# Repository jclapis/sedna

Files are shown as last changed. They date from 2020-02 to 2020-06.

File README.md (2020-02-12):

## Welcome to GitHub Pages

You can use the [editor on GitHub](https://github.com/jclapis/sedna/edit/master/README.md) to maintain and preview the content for your website in Markdown files.

Whenever you commit to this repository, GitHub Pages will run [Jekyll](https://jekyllrb.com/) to rebuild the pages in your site, from the content in your Markdown files.

### Markdown

Markdown is a lightweight and easy-to-use syntax for styling your writing. It includes conventions for

```markdown
Syntax highlighted code block

# Header 1
## Header 2
### Header 3

- Bulleted
- List

1. Numbered
2. List

**Bold** and _Italic_ and `Code` text

[Link](url) and ![Image](src)
```

For more details see [GitHub Flavored Markdown](https://guides.github.com/features/mastering-markdown/).

### Jekyll Themes

Your Pages site will use the layout and styles from the Jekyll theme you have selected in your [repository settings](https://github.com/jclapis/sedna/settings). The name of this theme is saved in the Jekyll `_config.yml` configuration file.

### Support or Contact

Having trouble with Pages? Check out our [documentation](https://help.github.com/categories/github-pages-basics/) or [contact support](https://github.com/contact) and we’ll help you sort it out.

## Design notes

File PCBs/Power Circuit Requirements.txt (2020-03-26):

Circuit requirements!

- An arbitrary 12v input
	- From a battery i'll make later
	- From the wall

- 12v line (motor, monitor)
- 7.2v line (camera)
- 5v line (pi, AMT22)
- 3.3v comes from the Pi for all of the other ICs
	- L6983CQTR for 12 and 7.2
	- L6983C50QTR for 5

- Measure rail voltages
	- MCP3208 (https://www.mouser.com/ProductDetail/Microchip-Technology/MCP3208T-CI-SL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)

- Current sensing shunt to see what the total current pull is
	- CS70P
		https://www.mouser.com/ProductDetail/STMicroelectronics/CS70P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
	- Resistor = 0.012 ohm, 500 mW
		https://www.mouser.com/ProductDetail/Vishay-Dale/WSK1206R0120FEA18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

- Thermometer
	- TC77-3.3MOA
		https://www.mouser.com/ProductDetail/Microchip-Technology/TC77-33MOA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

- Fuses?

NEED DECOUPLING CAPACITORS - 1uF ON EACH VDD PIN

SPRING TERMINALS: EATON EM2795 SERIES (Vertical is way cheaper for some reason)
	2-pin = EM279502V: https://www.mouser.com/ProductDetail/Bussmann-Eaton/EM279502V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
	The rest is stupidly expensive so just build it all out of these.

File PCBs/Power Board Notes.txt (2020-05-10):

** Assuming between 12.5v and 36v in, 400 kHz **

R_FILT = https://www.mouser.com/ProductDetail/Panasonic/ERA-6AEB101V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

=== Output Voltage Resistors ===
For 12v line:
	619 / 47 => 12.0446809v
	R1 = 619k https://www.mouser.com/ProductDetail/Panasonic/ERA-6AEB6193V?qs=sGAEpiMZZMvdGkrng054txAO1F77ZlZQbHrViC3uPIQ%3D
	R2 = 47k https://www.mouser.com/ProductDetail/Panasonic/ERA-6AEB473V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

For 7.2v line:
	680 / 91 => 7.20165v
	R1 = 680k = https://www.mouser.com/ProductDetail/Panasonic/ERA-6AEB684V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
	R2 = 91k = https://www.mouser.com/ProductDetail/Panasonic/ERA-6AEB913V?qs=sGAEpiMZZMvdGkrng054tysRcmITJKxoen6wp78Btbg%3D

For 5v line:
	402 / 82 => 5.017073v
	R1 = 402k = https://www.mouser.com/ProductDetail/Panasonic/ERA-6AEB4023V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
	R2 = 82k = https://www.mouser.com/ProductDetail/Panasonic/ERA-6AEB823V?qs=sGAEpiMZZMvdGkrng054tysRcmITJKxoBfxHTzMcu7Q%3D

=== Main Inductor ===
For 12v line:
	Min = 6.53977
	Max = 39.2430
	Mid = 22.89 uH (go with 22)
		https://www.mouser.com/ProductDetail/Pulse-Electronics/PA4343223NLT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

For 7.2v line:
	Min = -5.460 (so 0)
	Max = 27.243
	Mid = 13.6215 uH (go with 15)
		https://www.mouser.com/ProductDetail/Pulse-Electronics/PM4343153NLT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

For 5v line:
	Min = -10.9602 (so 0)
	Max = 21.7430
	Mid = 10.8715 uH (go with 10)
		https://www.mouser.com/ProductDetail/Pulse-Electronics/PM4343103NLT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

=== Output Capacitor ===
For 12v line:
	Min = 13.4 uF
	Max = 80 uF
	Mid = 46.7
		47 (26.5839) + 22 (18.5890) = 69 (45.1729)
		47 = https://www.mouser.com/ProductDetail/TDK/C5750X5R1C476M230KA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
		22 = https://www.mouser.com/ProductDetail/TDK/C5750X5R1E226M250KA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

For 7.2v line:
	Min = 22.3 uF
	Max = 133.3 uF
	Mid = 77.8
		47 (37.9989) + 47 (37.9989) = 94 (75.9978)
		47 = https://www.mouser.com/ProductDetail/TDK/C5750X5R1C476M230KA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

For 5v line:
	Min = 32.16 uF
	Max = 192 uF
	Mid = 112.08
		47 (43.3823) + 47 (43.3823) = 94 (86.7646), good enough
		47 = https://www.mouser.com/ProductDetail/TDK/C5750X5R1C476M230KA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

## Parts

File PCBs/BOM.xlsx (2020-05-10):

Totals
Part | Model # | Link | Total
C_BOOT | CGA4J2X7R1H104K125AA | https://www.mouser.com/ProductDetail/TDK/CGA4J2X7R1H104K125AA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 | 3
C_FILT and C_VIN | CGA4J3X7R1H105K125AB | https://www.mouser.com/ProductDetail/TDK/CGA4J3X7R1H105K125AB | 9
C_IN | CGA5L3X5R1H106K160AB | https://www.mouser.com/ProductDetail/TDK/CGA5L3X5R1H106K160AB | 3
47uF C_OUT | C5750X5R1C476M230KA | https://www.mouser.com/ProductDetail/TDK/C5750X5R1C476M230KA | 5
22uF C_OUT | C5750X5R1E226M250KA | https://www.mouser.com/ProductDetail/TDK/C5750X5R1E226M250KA | 1
C_VCC | CGA4J2X7R1C105K125AA | https://www.mouser.com/ProductDetail/TDK/CGA4J2X7R1C105K125AA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 | 3
5v Inductor | PM4343.103NLT | https://www.mouser.com/ProductDetail/Pulse-Electronics/PM4343103NLT | 1
7.2v Inductor | PM4343.153NLT | https://www.mouser.com/ProductDetail/Pulse-Electronics/PM4343153NLT | 1
12v Inductor | PA4343.223NLT | https://www.mouser.com/ProductDetail/Pulse-Electronics/PA4343223NLT | 1
Power Connectors | EM279502V | https://www.mouser.com/ProductDetail/Bussmann-Eaton/EM279502V | 6
L6983 | L6983CQTR | https://www.mouser.com/ProductDetail/STMicroelectronics/L6983CQTR | 3
5v FBH Resistor | ERA-6AEB4023V | https://www.mouser.com/ProductDetail/Panasonic/ERA-6AEB4023V | 1
5v FBL Resistor | ERA-6AEB823V | https://www.mouser.com/ProductDetail/Panasonic/ERA-6AEB823V?qs=sGAEpiMZZMvdGkrng054tysRcmITJKxoBfxHTzMcu7Q%3D | 1
7.2v FBH Resistor | ERA-6AEB684V | https://www.mouser.com/ProductDetail/Panasonic/ERA-6AEB684V | 1
7.2v FBL Resistor | ERA-6AEB913V | https://www.mouser.com/ProductDetail/Panasonic/ERA-6AEB913V?qs=sGAEpiMZZMvdGkrng054tysRcmITJKxoen6wp78Btbg%3D | 1
12v FBH Resistor | ERA-6AEB6193V | https://www.mouser.com/ProductDetail/Panasonic/ERA-6AEB6193V?qs=sGAEpiMZZMvdGkrng054txAO1F77ZlZQbHrViC3uPIQ%3D | 1
12v FBL Resistor | ERA-6AEB473V | https://www.mouser.com/ProductDetail/Panasonic/ERA-6AEB473V | 1
R_FILT | ERA-6AEB101V | https://www.mouser.com/ProductDetail/Panasonic/ERA-6AEB101V | 3
R_PGOOD | ERA-6AEB105V | https://www.mouser.com/ProductDetail/Panasonic/ERA-6AEB105V | 3

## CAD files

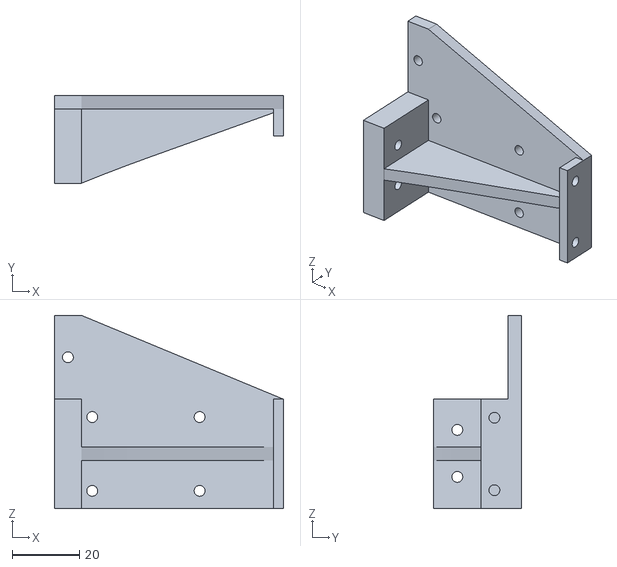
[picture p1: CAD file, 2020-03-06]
CAD Models/Focusing Assembly/Coupling Hub.stl
68.2 x 26.1 x 57.6

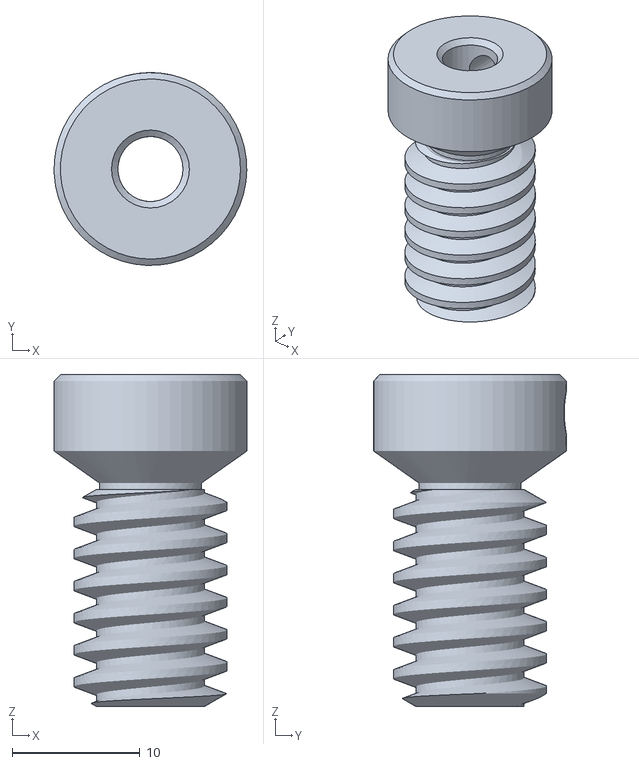
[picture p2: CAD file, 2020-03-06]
CAD Models/Focusing Assembly/Worm.stl
15.1 x 15.1 x 26.0

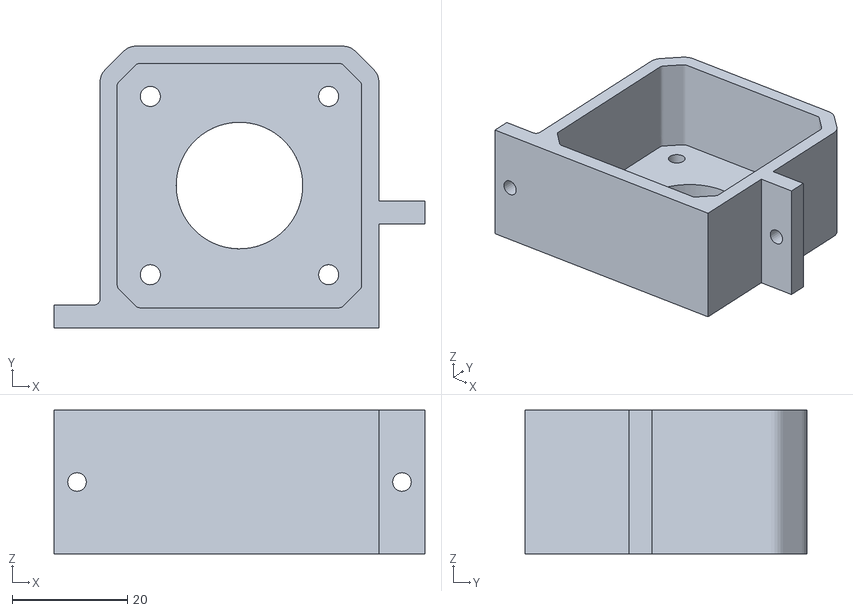
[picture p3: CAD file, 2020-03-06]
CAD Models/Focusing Assembly/Motor Housing.stl
64.5 x 49.0 x 25.0

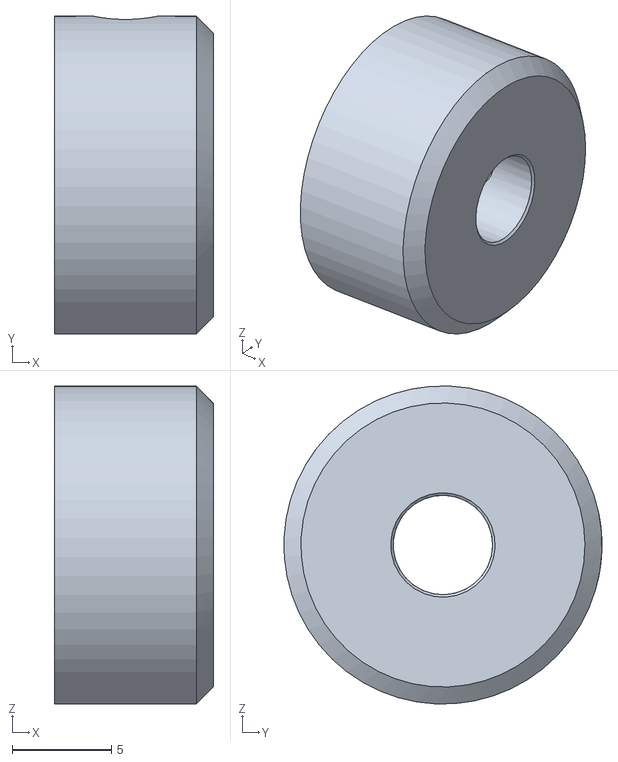
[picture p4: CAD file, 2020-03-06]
CAD Models/Focusing Assembly/Spur Gear Back.stl
8.00 x 16.0 x 16.0

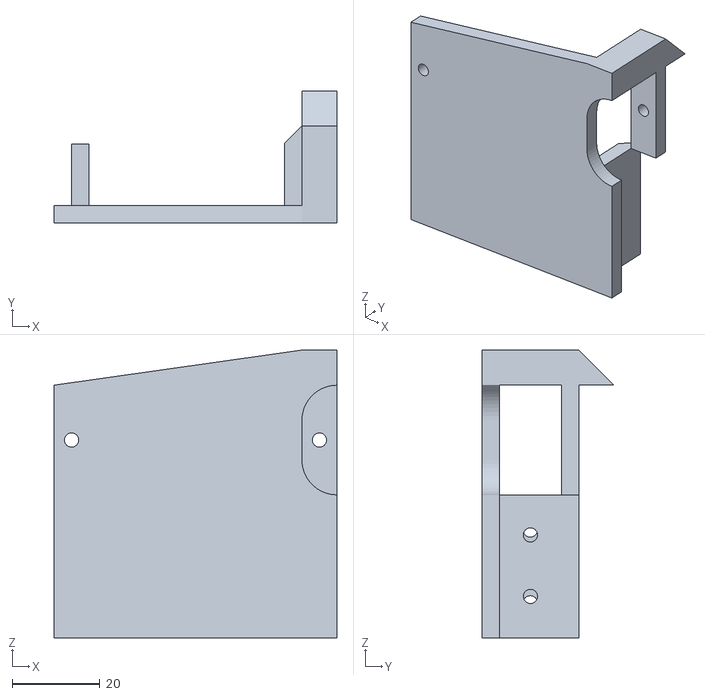
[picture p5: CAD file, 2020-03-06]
CAD Models/Focusing Assembly/Base Plate.stl
64.5 x 30.1 x 65.6

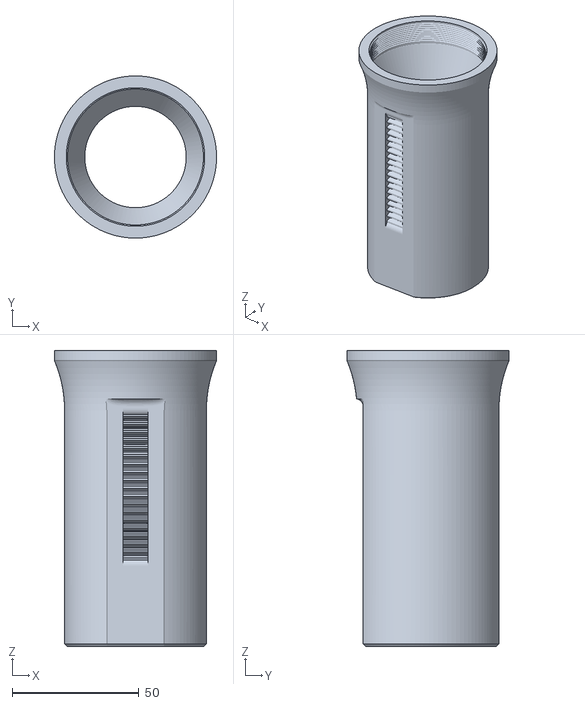
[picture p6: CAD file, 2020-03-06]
CAD Models/Focusing Assembly/Optical Tube.stl
64.0 x 64.0 x 116.8

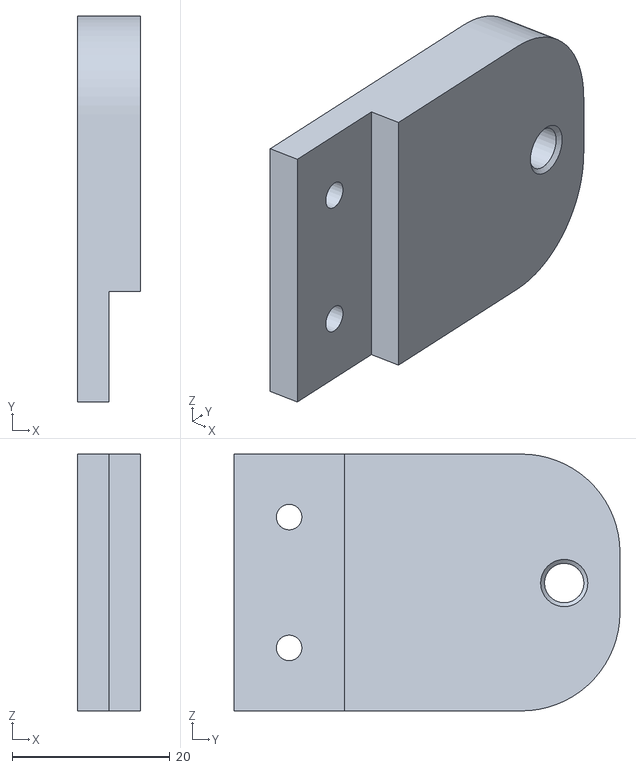
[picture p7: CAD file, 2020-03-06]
CAD Models/Focusing Assembly/Retainer Arm.stl
8.00 x 49.0 x 32.6

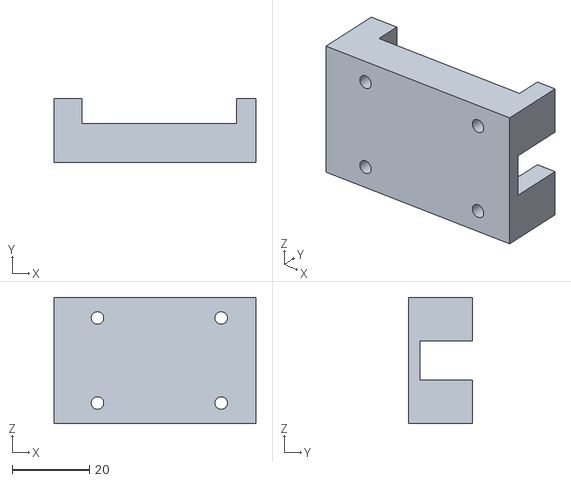
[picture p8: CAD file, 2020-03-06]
CAD Models/Focusing Assembly/Telescope Attachment.stl
52.2 x 16.5 x 32.6

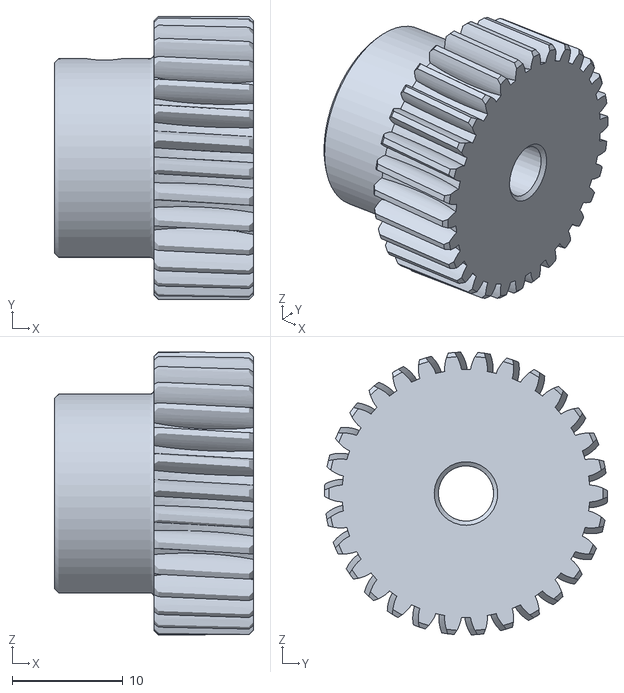
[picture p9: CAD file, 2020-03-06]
CAD Models/Focusing Assembly/Worm Gear.stl
18.0 x 25.6 x 25.6

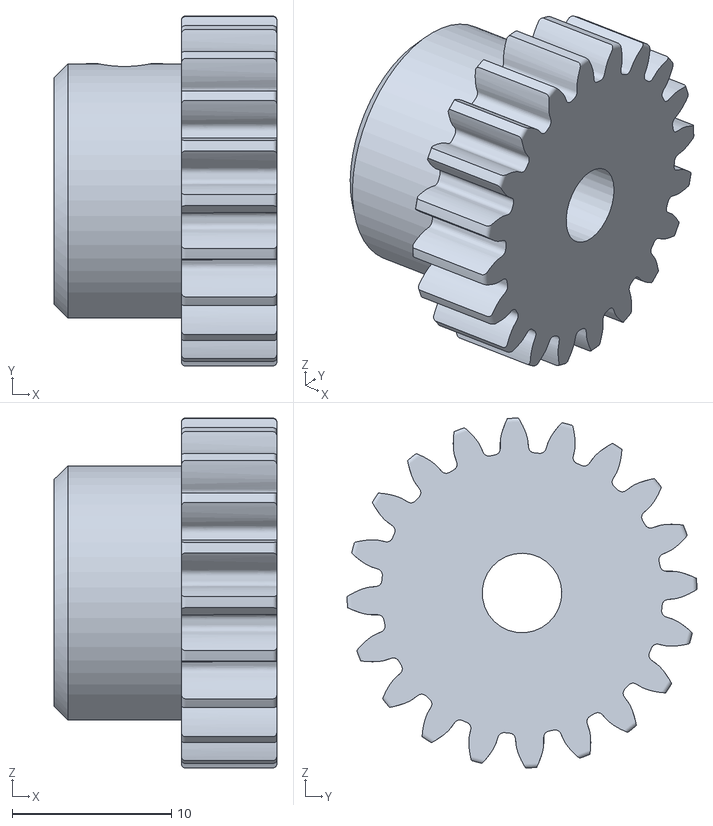
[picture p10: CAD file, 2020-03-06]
CAD Models/Focusing Assembly/Spur Gear.stl
14.0 x 22.0 x 22.0

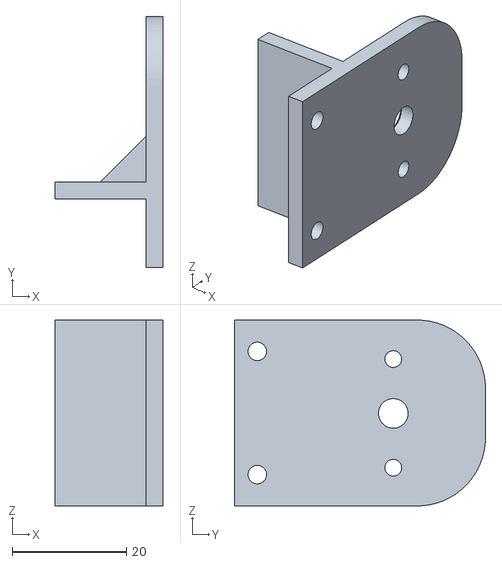
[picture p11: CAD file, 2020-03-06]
CAD Models/Focusing Assembly/AMT22 Bracket.stl
19.0 x 44.0 x 32.6

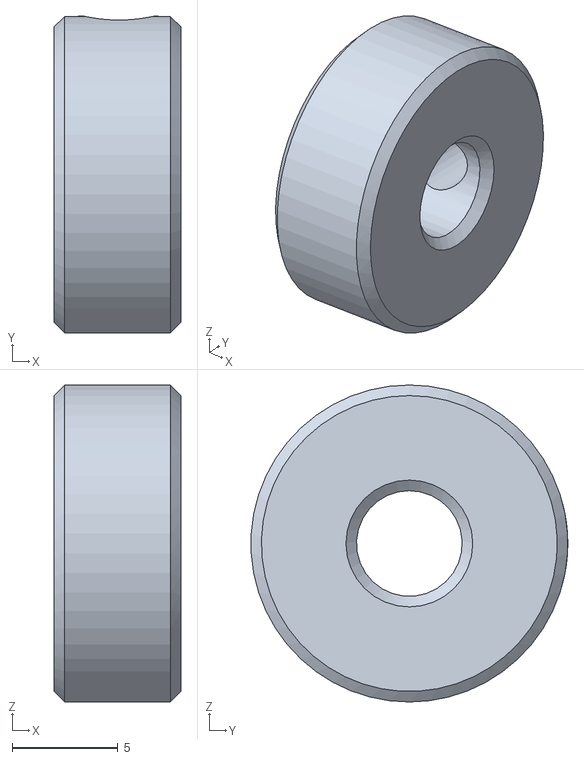
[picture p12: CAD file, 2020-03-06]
CAD Models/Focusing Assembly/Drive Shaft Washer.stl
6.00 x 15.0 x 15.0

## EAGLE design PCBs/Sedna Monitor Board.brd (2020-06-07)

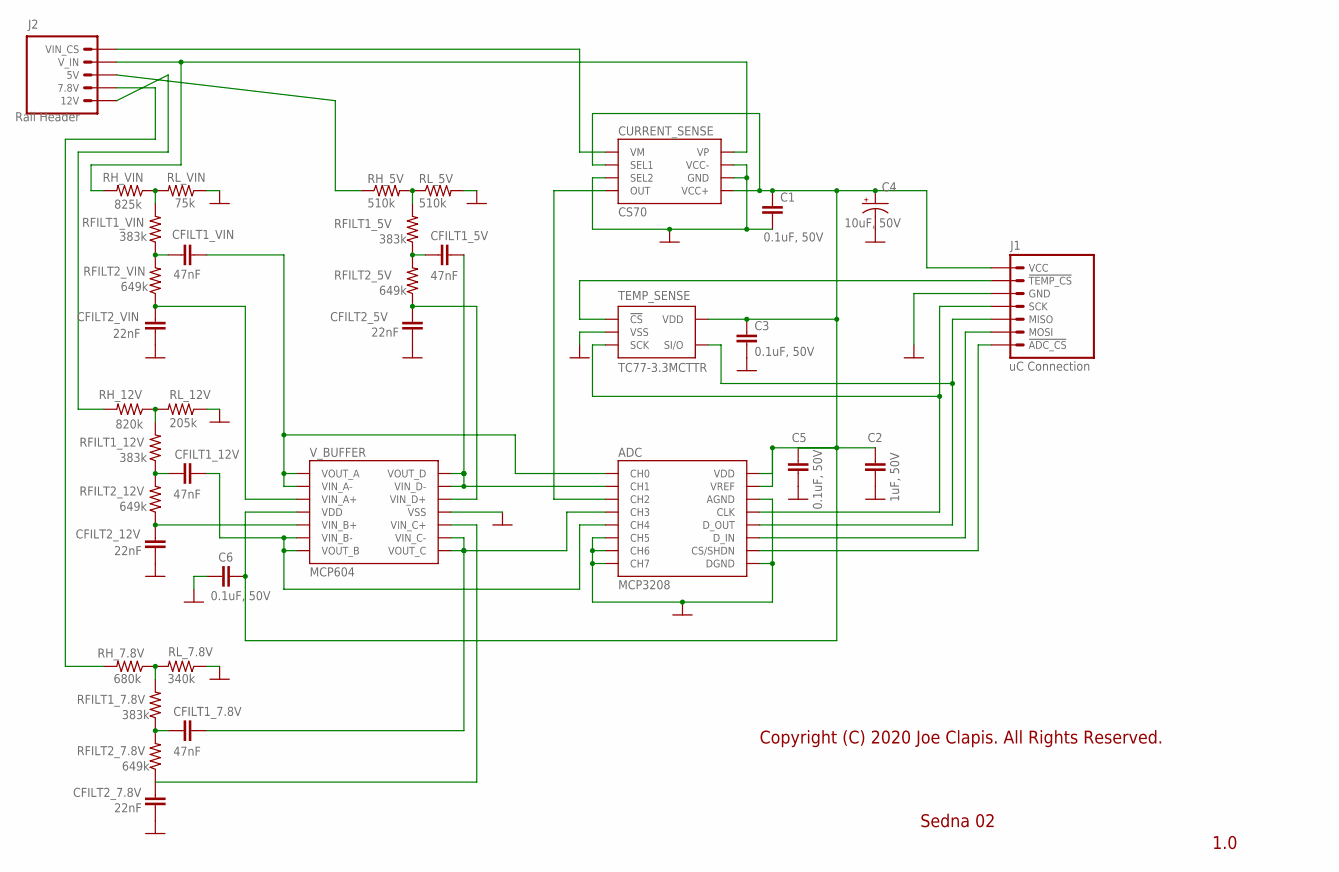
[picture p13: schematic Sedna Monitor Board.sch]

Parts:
ADC: MCP3208; MICROCHIP_SOIC-16_SL
C1, C3, C5, C6: 0.1uF, 50V; C0805
C2: 1uF, 50V; C0805
C4: 10uF, 50V; PANASONIC-SMD-CAP-SV-D
CFILT1_5V, CFILT1_7.8V, CFILT1_12V, CFILT1_VIN: 47nF; C0805
CFILT2_5V, CFILT2_7.8V, CFILT2_12V, CFILT2_VIN: 22nF; C0805
CURRENT_SENSE: CS70; TSSOP8
J1: uC Connection; 1X07
J2: Rail Header; 1X05
RFILT1_5V, RFILT1_7.8V, RFILT1_12V, RFILT1_VIN: 383k; R0805
RFILT2_5V, RFILT2_7.8V, RFILT2_12V, RFILT2_VIN: 649k; R0805
RH_5V: 510k; R0805
RH_7.8V: 680k; R0805
RH_12V: 820k; R0805
RH_VIN: 825k; R0805
RL_5V: 510k; R0805
RL_7.8V: 340k; R0805
RL_12V: 205k; R0805
RL_VIN: 75k; R0805
TEMP_SENSE: TC77-3.3MCTTR; MICROCHIP_SOT-23_5_OT
V_BUFFER: MCP604; MICROCHIP_TSSOP-14_ST

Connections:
ADC_CS: ADC.10 (CS/SHDN), J1.7 (!ADC_CS)
CS_OUT: ADC.3 (CH2), CURRENT_SENSE.4 (OUT)
GND: ADC.6 (CH5), ADC.7 (CH6), ADC.8 (CH7), ADC.9 (DGND), ADC.14 (AGND), C1.2, C2.2, C3.2, C4.GND (-), C5.2, C6.2, CFILT2_5V.1, CFILT2_7.8V.1, CFILT2_12V.1, CFILT2_VIN.1, CURRENT_SENSE.3 (SEL2), CURRENT_SENSE.6 (GND), CURRENT_SENSE.7 (VCC-), J1.3 (GND), RL_5V.2, RL_7.8V.1, RL_12V.1, RL_VIN.1, TEMP_SENSE.2 (VSS), V_BUFFER.11 (VSS)
MOSI: ADC.11 (D_IN), J1.6 (MOSI)
unnamed: ADC.12 (D_OUT), J1.5 (MISO), TEMP_SENSE.4 (SI/O)
unnamed: CURRENT_SENSE.1 (VM), J2.1 (VIN_CS)
unnamed: CURRENT_SENSE.8 (VP), J2.2 (V_IN), RH_VIN.2
unnamed: J2.4 (7.8V), RH_7.8V.2
unnamed: J2.3 (5V), RH_5V.1
unnamed: RFILT1_12V.2, RH_12V.1, RL_12V.2
unnamed: CFILT2_VIN.2, RFILT2_VIN.1, V_BUFFER.3 (VIN_A+)
unnamed: CFILT1_VIN.1, RFILT1_VIN.1, RFILT2_VIN.2
unnamed: J2.5 (12V), RH_12V.2
unnamed: RFILT1_VIN.2, RH_VIN.1, RL_VIN.2
unnamed: CFILT2_12V.2, RFILT2_12V.1, V_BUFFER.5 (VIN_B+)
unnamed: CFILT1_7.8V.2, RFILT1_7.8V.1, RFILT2_7.8V.2
unnamed: CFILT2_7.8V.2, RFILT2_7.8V.1, V_BUFFER.10 (VIN_C+)
unnamed: RFILT1_7.8V.2, RH_7.8V.1, RL_7.8V.2
unnamed: CFILT1_12V.1, RFILT1_12V.1, RFILT2_12V.2
unnamed: RFILT1_5V.2, RH_5V.2, RL_5V.1
unnamed: CFILT1_5V.2, RFILT1_5V.1, RFILT2_5V.2
unnamed: CFILT2_5V.2, RFILT2_5V.1, V_BUFFER.12 (VIN_D+)
SCK: ADC.13 (CLK), J1.4 (SCK), TEMP_SENSE.3 (SCK)
TC77_CS: J1.2 (!TEMP_CS), TEMP_SENSE.1 (!CS)
VDD: ADC.15 (VREF), ADC.16 (VDD), C1.1, C2.1, C3.1, C4.VDD (+), C5.1, C6.1, CURRENT_SENSE.2 (SEL1), CURRENT_SENSE.5 (VCC+), J1.1 (VCC), TEMP_SENSE.5 (VDD), V_BUFFER.4 (VDD)
VOUT_A: ADC.1 (CH0), CFILT1_VIN.2, V_BUFFER.1 (VOUT_A), V_BUFFER.2 (VIN_A-)
VOUT_B: ADC.5 (CH4), CFILT1_12V.2, V_BUFFER.6 (VIN_B-), V_BUFFER.7 (VOUT_B)
VOUT_C: ADC.4 (CH3), CFILT1_7.8V.1, V_BUFFER.8 (VOUT_C), V_BUFFER.9 (VIN_C-)
VOUT_D: ADC.2 (CH1), CFILT1_5V.1, V_BUFFER.13 (VIN_D-), V_BUFFER.14 (VOUT_D)

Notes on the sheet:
Sedna 02
1.0
Copyright (C) 2020 Joe Clapis. All Rights Reserved.

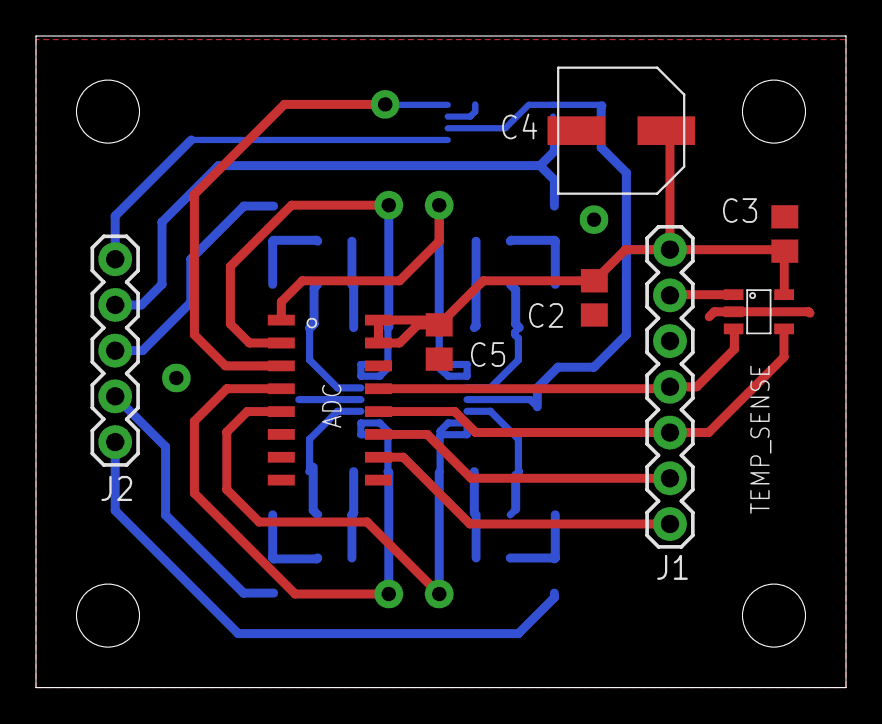
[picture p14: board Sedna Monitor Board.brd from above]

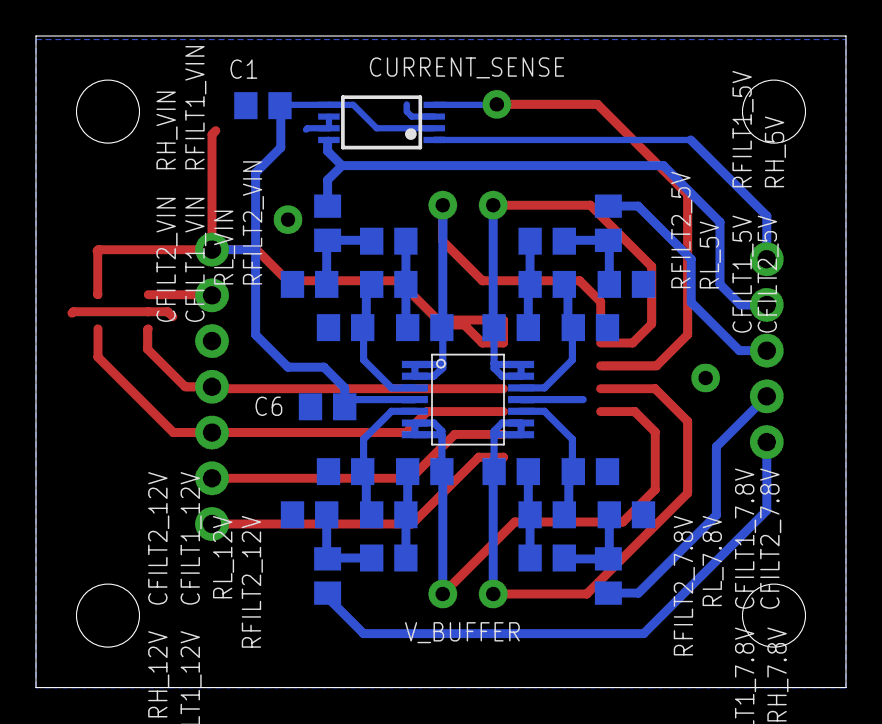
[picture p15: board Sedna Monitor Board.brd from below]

Board: 2 copper layers, 45.0 x 36.2 mm, 36 parts (28 on the bottom side), 29 nets.

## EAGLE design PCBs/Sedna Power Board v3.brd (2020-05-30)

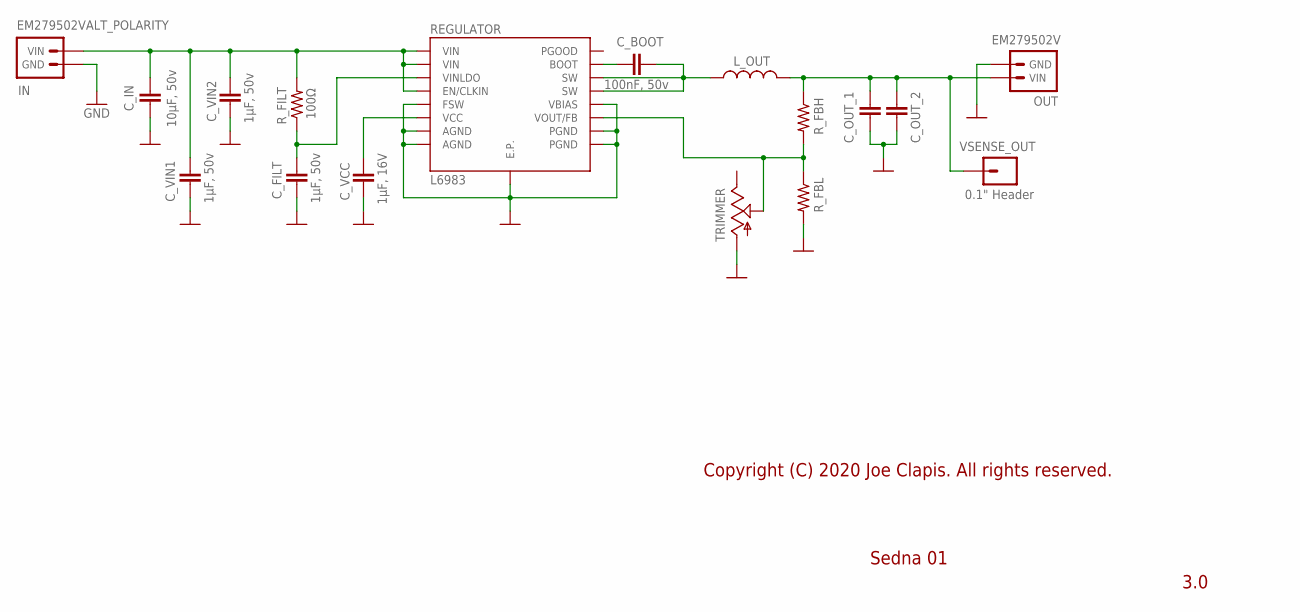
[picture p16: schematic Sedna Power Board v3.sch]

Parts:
C_BOOT: 100nF, 50v; C0805
C_FILT: 1μF, 50v; C0805
C_IN: 10μF, 50v; C1206
C_OUT_1, C_OUT_2: TDK_C2220_5750
C_VCC: 1μF, 16V; C0805
C_VIN1, C_VIN2: 1μF, 50v; C0805
IN: EM279502VALT_POLARITY; EM279502V
L_OUT: PA4343_FP2
OUT: EM279502V
REGULATOR: L6983
R_FBH: R-US_R0805; R0805
R_FBL: R-US_R0805; R0805
R_FILT: 100Ω; R0805
TRIMMER: BOURNS_3361S
VSENSE_OUT: 0.1" Header; 1X01

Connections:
C_BOOT: C_BOOT.1, REGULATOR.11_BOOT (BOOT)
FB: REGULATOR.7_FB/VOUT (VOUT/FB), R_FBH.2, R_FBL.1, TRIMMER.2 (S)
GND: C_FILT.2, C_IN.2, C_OUT_1.2, C_OUT_2.2, C_VCC.2, C_VIN1.2, C_VIN2.2, IN.1A (GND), IN.1B (GND), OUT.2A (GND), OUT.2B (GND), REGULATOR.3_AGND (AGND), REGULATOR.6_VBIAS (VBIAS), REGULATOR.8_FSW (FSW), REGULATOR.10_AGND (AGND), REGULATOR.13_PGND (PGND), REGULATOR.16_PGND (PGND), REGULATOR.E.P., R_FBL.2, TRIMMER.1 (A)
SW_OUT: C_BOOT.2, L_OUT.1, REGULATOR.14_SW (SW), REGULATOR.15_SW (SW)
VCC: C_VCC.1, REGULATOR.9_VCC (VCC)
VINLDO: C_FILT.1, REGULATOR.2_VINLDO (VINLDO), R_FILT.1
V_IN: C_IN.1, C_VIN1.1, C_VIN2.1, IN.2A (VIN), IN.2B (VIN), REGULATOR.1_VIN (VIN), REGULATOR.4_EN/CLKIN (EN/CLKIN), REGULATOR.12_VIN (VIN), R_FILT.2
V_OUT: C_OUT_1.1, C_OUT_2.1, L_OUT.2, OUT.1A (VIN), OUT.1B (VIN), R_FBH.1, VSENSE_OUT.1

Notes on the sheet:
Sedna 01
3.0
Copyright (C) 2020 Joe Clapis. All rights reserved.

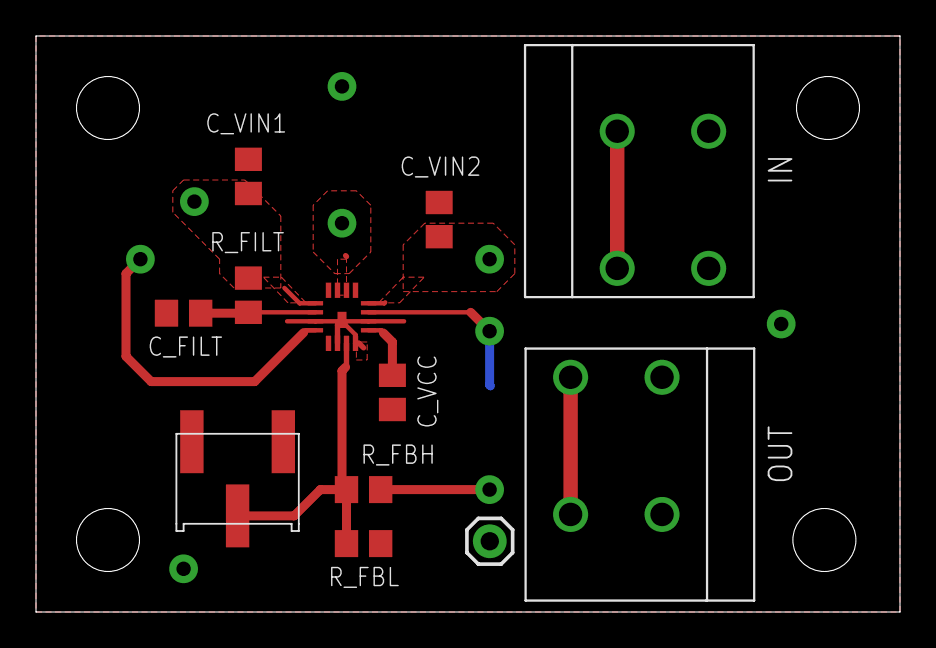
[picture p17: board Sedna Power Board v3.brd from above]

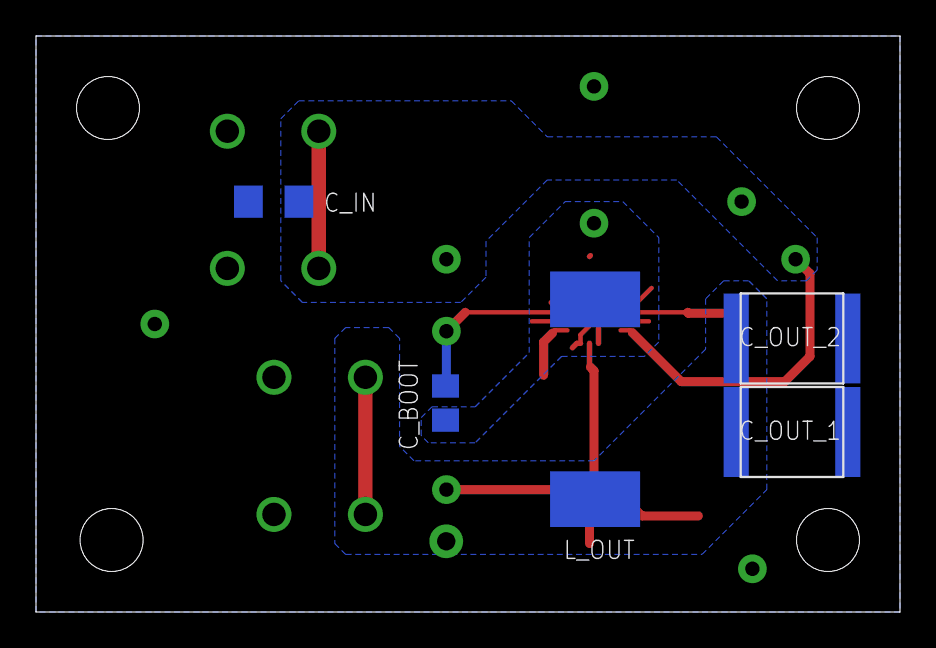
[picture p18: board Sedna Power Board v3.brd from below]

Board: 2 copper layers, 48.0 x 32.0 mm, 17 parts (5 on the bottom side), 8 nets.

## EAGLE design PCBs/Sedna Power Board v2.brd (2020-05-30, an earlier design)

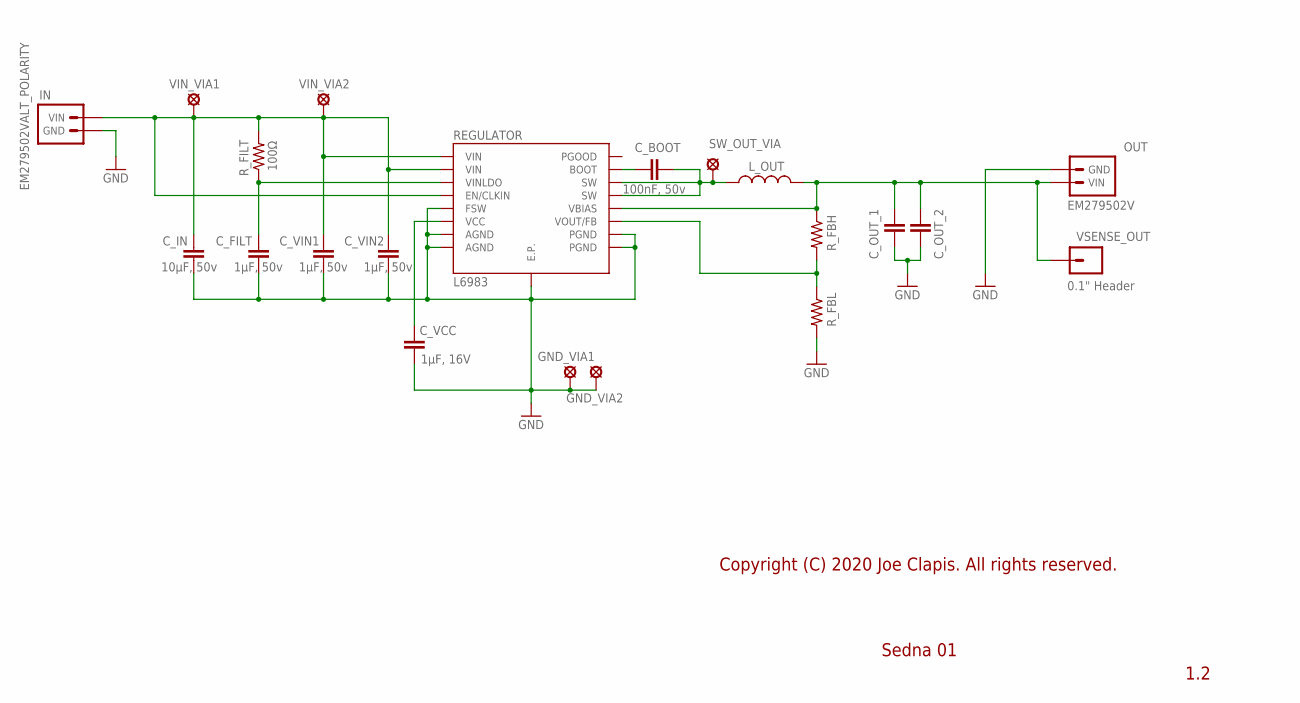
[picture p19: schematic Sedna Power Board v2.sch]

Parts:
C_BOOT: 100nF, 50v; C0805
C_FILT: 1μF, 50v; C0805
C_IN: 10μF, 50v; C1206
C_OUT_1, C_OUT_2: TDK_C2220_5750
C_VCC: 1μF, 16V; C0805
C_VIN1, C_VIN2: 1μF, 50v; C0805
GND_VIA1, GND_VIA2: LSP13
IN: EM279502VALT_POLARITY; EM279502V
L_OUT: PA4343_FP2
OUT: EM279502V
REGULATOR: L6983
R_FBH: R-US_R0805; R0805
R_FBL: R-US_R0805; R0805
R_FILT: 100Ω; R0805
SW_OUT_VIA: LSP13
VIN_VIA1, VIN_VIA2: LSP13
VSENSE_OUT: 0.1" Header; 1X01

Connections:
C_BOOT: C_BOOT.1, REGULATOR.11_BOOT (BOOT)
FB: REGULATOR.7_FB/VOUT (VOUT/FB), R_FBH.2, R_FBL.1
GND: C_FILT.2, C_IN.2, C_OUT_1.2, C_OUT_2.2, C_VCC.2, C_VIN1.2, C_VIN2.2, GND_VIA1.MP, GND_VIA2.MP, IN.1A (GND), IN.1B (GND), OUT.2A (GND), OUT.2B (GND), REGULATOR.3_AGND (AGND), REGULATOR.8_FSW (FSW), REGULATOR.10_AGND (AGND), REGULATOR.13_PGND (PGND), REGULATOR.16_PGND (PGND), REGULATOR.E.P., R_FBL.2
SW_OUT: C_BOOT.2, L_OUT.1, REGULATOR.14_SW (SW), REGULATOR.15_SW (SW), SW_OUT_VIA.MP
VCC: C_VCC.1, REGULATOR.9_VCC (VCC)
VINLDO: C_FILT.1, REGULATOR.2_VINLDO (VINLDO), R_FILT.1
V_IN: C_IN.1, C_VIN1.1, C_VIN2.1, IN.2A (VIN), IN.2B (VIN), REGULATOR.1_VIN (VIN), REGULATOR.4_EN/CLKIN (EN/CLKIN), REGULATOR.12_VIN (VIN), R_FILT.2, VIN_VIA1.MP, VIN_VIA2.MP
V_OUT: C_OUT_1.1, C_OUT_2.1, L_OUT.2, OUT.1A (VIN), OUT.1B (VIN), REGULATOR.6_VBIAS (VBIAS), R_FBH.1, VSENSE_OUT.1

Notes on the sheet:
Sedna 01
1.2
Copyright (C) 2020 Joe Clapis. All rights reserved.

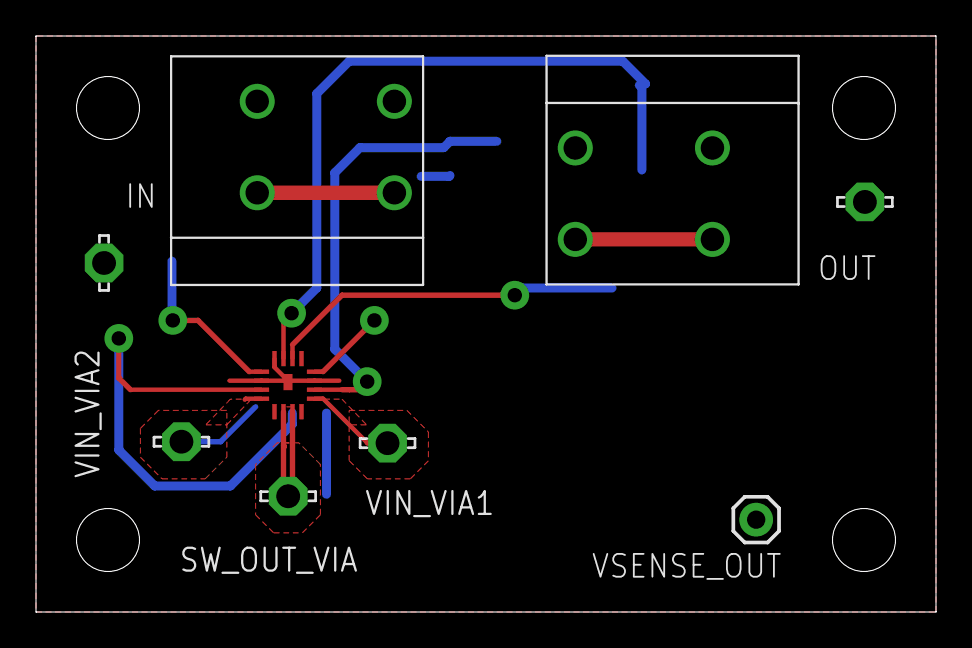
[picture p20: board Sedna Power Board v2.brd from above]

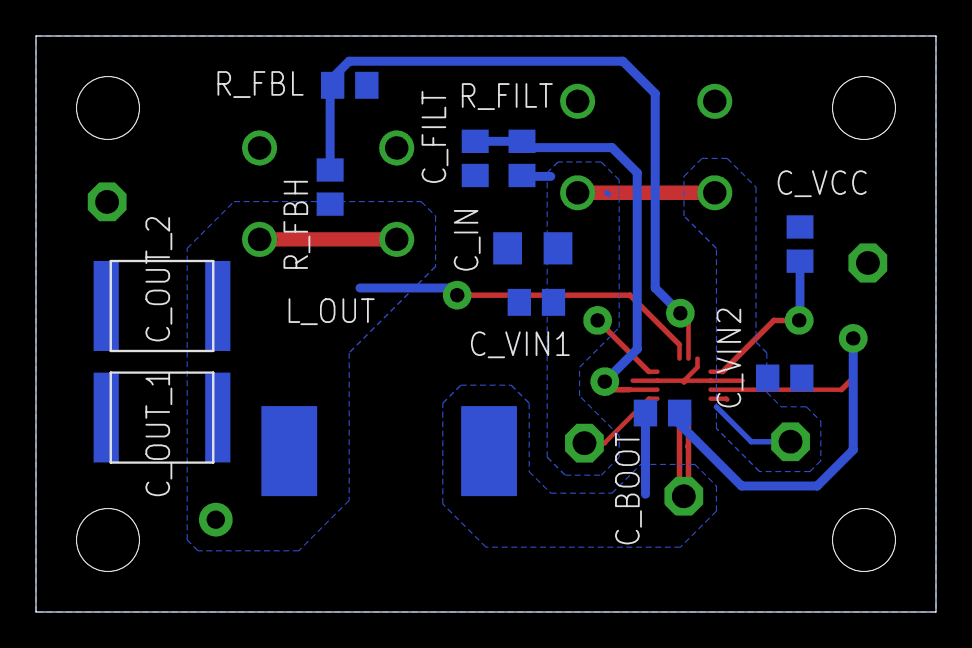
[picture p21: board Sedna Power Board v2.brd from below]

Board: 2 copper layers, 50.0 x 32.0 mm, 21 parts (12 on the bottom side), 8 nets.

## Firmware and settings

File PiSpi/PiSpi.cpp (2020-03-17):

/* ========================================================================
 * Copyright (C) 2020 Joe Clapis.
 *
 * Licensed under the Apache License, Version 2.0 (the "License");
 * you may not use this file except in compliance with the License.
 * You may obtain a copy of the License at
 *
 *     http://www.apache.org/licenses/LICENSE-2.0
 *
 * Unless required by applicable law or agreed to in writing, software
 * distributed under the License is distributed on an "AS IS" BASIS,
 * WITHOUT WARRANTIES OR CONDITIONS OF ANY KIND, either express or implied.
 * See the License for the specific language governing permissions and
 * limitations under the License.
 * ======================================================================== */

// Import the spidev header as C, otherwise the mode macros (e.g. SPI_IOC_RD_MODE)
// won't always work. Shoutout to Phil Mills on StackOverflow for figuring this out:
// https://stackoverflow.com/questions/31572738/spi-ioc-messagen-macro-giving-me-fits
extern "C"
{
    #include <linux/spi/spidev.h>
}

#include <stdio.h>
#include <fcntl.h>
#include <string.h>
#include <errno.h>
#include <sys/ioctl.h>
#include <asm/ioctl.h>
#include <wiringPi.h>
#include "PiSpi.h"


// This will hold the error message of the last error
static char LastErrorMessage[1024];


// Sets the last error message based on what happened during the error
static void SetLastError(const char* Message)
{
    int lastErrorCode = errno;
    snprintf(LastErrorMessage, 1024, "%s: %s (%d)", Message, strerror(lastErrorCode), lastErrorCode);
}


// The FD for SPI hardware device 0
static int SpiDevDescriptor;


// The underlying device struct
struct SpiDevice
{
    uint8_t ChipSelectPin;
    uint32_t BitRate;
    int Mode;
    uint8_t TimeBeforeRead;
    uint8_t TimeBetweenBytes;
    uint8_t TimeAfterRead;
    uint8_t TimeBetweenReads;
};


PiSpi_Result PiSpi_CreateDevice(
    uint8_t ChipSelectPin,
    uint32_t BitRate,
    PiSpi_SpiMode Mode,
    uint8_t TimeBeforeRead,
    uint8_t TimeBetweenBytes,
    uint8_t TimeAfterRead,
    uint8_t TimeBetweenReads,
    void** Device)
{
    // Initialize the SPI bus when the first device is created
    if (SpiDevDescriptor == 0)
    {
        // Initialize WiringPi
        int result = wiringPiSetupSys();
        if (result == -1)
        {
            SetLastError("WiringPi failed to setup properly");
            return PiSpi_WiringPiInitFailed;
        }

        // Open the first SPI device for read-write, and tell it that we'll take care of the chip select
        // manually. This is necessary when you have more than 2 SPI devices, since the Pi only supports
        // 2 in hardware. We're going to do what's called a "software CS" in this library:
        // https://raspberrypi.stackexchange.com/questions/71448/how-to-connect-multiple-spi-devices-adcs-to-raspberry-pi
        SpiDevDescriptor = open("/dev/spidev0.0", O_RDWR | SPI_NO_CS);
        if (SpiDevDescriptor == -1)
        {
            SetLastError("Failed to open SPI Device 0 during bus initialization");
            return PiSpi_OpeningSpiDev0Failed;
        }

        // Set the bits per word to 8, which most SPI devices use. This is hardcoded for now because I
        // don't really plan to ever need to modify this; if I do, I'll have to come back here and fix it.
        int bitsPerWord = 8;
        result = ioctl(SpiDevDescriptor, SPI_IOC_WR_BITS_PER_WORD, &bitsPerWord);
        if (result == -1)
        {
            SetLastError("Failed to set the bits-per-word for the SPI bus during initialization");
            return PiSpi_SettingBitsPerWordFailed;
        }
    }

    // Define the chip select pin as an output and make sure it's not currently selected
    pinMode(ChipSelectPin, OUTPUT);
    digitalWrite(ChipSelectPin, HIGH);

    // Create the SPI device struct
    SpiDevice* device = new SpiDevice;
    device->ChipSelectPin = ChipSelectPin;
    device->BitRate = BitRate;
    device->Mode = Mode;
    device->TimeBeforeRead = TimeBeforeRead;
    device->TimeBetweenBytes = TimeBetweenBytes;
    device->TimeAfterRead = TimeAfterRead;
    device->TimeBetweenReads = TimeBetweenReads;
    *Device = device;

    return PiSpi_OK;
}


void PiSpi_FreeDevice(void* Device)
{
    SpiDevice* device = static_cast<SpiDevice*>(Device);
    if (device != nullptr)
    {
        delete device;
    }
}


PiSpi_Result RunTransferWithoutDelaysBetweenBytes(SpiDevice* Device, uint8_t* Buffer, uint32_t BufferSize)
{
    // Set up the SPI transfer structure
    __u64 bufferAsLong = reinterpret_cast<__u64>(Buffer);
    spi_ioc_transfer spiTransfer;
    memset(&spiTransfer, 0, sizeof(spiTransfer));

    spiTransfer.speed_hz = Device->BitRate;
    spiTransfer.len = static_cast<__u32>(BufferSize);
    spiTransfer.rx_buf = bufferAsLong;
    spiTransfer.tx_buf = bufferAsLong;

    // Run the transfer
    int result = ioctl(SpiDevDescriptor, SPI_IOC_MESSAGE(1), &spiTransfer);
    if (result == -1)
    {
        SetLastError("Error transferring data to/from the SPI device");
        return PiSpi_SpiTransferFailed;
    }

    return PiSpi_OK;
}


PiSpi_Result RunTransferWithDelaysBetweenBytes(SpiDevice* Device, uint8_t* Buffer, uint32_t BufferSize)
{
    spi_ioc_transfer spiTransfer;
    memset(&spiTransfer, 0, sizeof(spiTransfer));
    spiTransfer.speed_hz = Device->BitRate;
    for (int i = 0; i < BufferSize; i++)
    {
        // Set up the transfer structure
        uint8_t* currentBufferBytePointer = Buffer + i;
        __u64 bufferAsLong = reinterpret_cast<__u64>(currentBufferBytePointer);
        spiTransfer.len = static_cast<__u32>(sizeof(uint8_t));
        spiTransfer.rx_buf = bufferAsLong;
        spiTransfer.tx_buf = bufferAsLong;

        // Run the transfer
        int result = ioctl(SpiDevDescriptor, SPI_IOC_MESSAGE(1), &spiTransfer);
        if (result == -1)
        {
            SetLastError("Error transferring data to/from the SPI device");
            return PiSpi_SpiTransferFailed;
        }

        // Wait for the specified time between bytes
        delayMicroseconds(Device->TimeBetweenBytes);
    }

    return PiSpi_OK;
}
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

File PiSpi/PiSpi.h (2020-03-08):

/* ========================================================================
 * Copyright (C) 2020 Joe Clapis.
 *
 * Licensed under the Apache License, Version 2.0 (the "License");
 * you may not use this file except in compliance with the License.
 * You may obtain a copy of the License at
 *
 *     http://www.apache.org/licenses/LICENSE-2.0
 *
 * Unless required by applicable law or agreed to in writing, software
 * distributed under the License is distributed on an "AS IS" BASIS,
 * WITHOUT WARRANTIES OR CONDITIONS OF ANY KIND, either express or implied.
 * See the License for the specific language governing permissions and
 * limitations under the License.
 * ======================================================================== */

#pragma once

#include <stdint.h>

#ifdef  __cplusplus
extern "C" {
#endif

	/// <summary>
	/// This defines what SPI mode a device uses.
	/// </summary>
	enum PiSpi_SpiMode
	{
		/// <summary>
		/// Mode 0 (clock polarity 0, clock phase 0, clock edge 1)
		/// </summary>
		PiSpi_SpiMode0 = SPI_MODE_0,

		/// <summary>
		/// Mode 1 (clock polarity 0, clock phase 1, clock edge 0)
		/// </summary>
		PiSpi_SpiMode1 = SPI_MODE_1,

		/// <summary>
		/// Mode 2 (clock polarity 1, clock phase 0, clock edge 1)
		/// </summary>
		PiSpi_SpiMode2 = SPI_MODE_2,

		/// <summary>
		/// Mode 3 (clock polarity 1, clock phase 1, clock edge 0)
		/// </summary>
		PiSpi_SpiMode3 = SPI_MODE_3
	};


	/// <summary>
	/// This defines the various return codes for PiSpi functions.
	/// </summary>
	enum PiSpi_Result
	{
		/// <summary>
		/// The function succeeded.
		/// </summary>
		PiSpi_OK = 0,

		/// <summary>
		/// Initializing WiringPi failed.
		/// </summary>
		PiSpi_WiringPiInitFailed = -1,

		/// <summary>
		/// Opening SPI device 0 (/dev/spidev0.0) failed.
		/// </summary>
		PiSpi_OpeningSpiDev0Failed = -2,

		/// <summary>
		/// Setting the bits-per-word for the SPI bus failed.
		/// </summary>
		PiSpi_SettingBitsPerWordFailed = -3,

		/// <summary>
		/// Setting the SPI mode for a transfer failed.
		/// </summary>
		PiSpi_SettingSpiModeFailed = -4,

		/// <summary>
		/// Transferring data over the SPI bus failed.
		/// </summary>
		PiSpi_SpiTransferFailed = -5
	};


	/// <summary>
	/// Creates a new SPI device. This will use the standard SPI device 0 pins for SCLK, MISO, and MOSI.
	/// It will also initialize the chip select pin to output mode and set it HIGH.
	/// </summary>
	/// <param name="ChipSelectPin">The number of the chip select pin for this device. This uses the
	/// WiringPi pin layout. To find what the pin number is for a given physical pin, run `gpio readall`
	/// on your Pi.</param>
	/// <param name="BitRate">The speed of the SPI communications for this device, in Hz.</param>
	/// <param name="Mode">The SPI mode that this device uses</param>
	/// <param name="TimeBeforeRead">The delay (in microseconds) between pulling the chip select pin low
	/// and starting to read/write data from/to the device.</param>
	/// <param name="TimeBetweenBytes">The delay (in microseconds) to wait between reading and writing
	/// individual bytes. Some devices have specific timings for this; consult your device's datasheet.
	/// </param>
	/// <param name="TimeAfterRead">The delay (in microseconds) to wait after finishing a data read/write
	/// before setting the chip select pin back to high (unselecting the device).</param>
	/// <param name="TimeBetweenReads">The delay (in microseconds) to wait after unselecting a device before
	/// it can be selected again for a subsequent read/write.</param>
	/// <param name="Device">[OUT] A handle to the new device.</param>
	/// <returns>PiSpi_OK on a success, or one of the error codes (all negative numbers) on a failure.
	/// Call PiSpi_GetLastError() for more information.</returns>
	PiSpi_Result PiSpi_CreateDevice(
		uint8_t ChipSelectPin,
		uint32_t BitRate,
		PiSpi_SpiMode Mode,
		uint8_t TimeBeforeRead,
		uint8_t TimeBetweenBytes,
		uint8_t TimeAfterRead,
		uint8_t TimeBetweenReads,
		void** Device
	);


	/// <summary>
	/// Deletes / frees a SPI device.
	/// </summary>
	/// <param name="Device">The device to free. This must have been created with PiSpi_CreateDevice().</param>
	void PiSpi_FreeDevice(void* Device);


	/// <summary>
	/// Transfers data to and from the SPI device in duplex mode.
	/// </summary>
	/// <param name="Device">A handle to a SPI device created by PiSpi_CreateDevice().</param>
	/// <param name="Buffer">The buffer containing the data to write. After the transfer, this will contain
	/// the data that was read from the device.</param>
	/// <param name="BufferSize">The size of the buffer, in bytes.</param>
	/// <returns>PiSpi_OK on a success, or one of the error codes (all negative numbers) on a failure.
	/// Call PiSpi_GetLastError() for more information.</returns>
	PiSpi_Result PiSpi_TransferData(void* Device, uint8_t* Buffer, uint32_t BufferSize);


	/// <summary>
	/// Returns an error message describing the last error that occurred.
	/// </summary>
	/// <returns>A human-readable description of the last error.</returns>
	const char* PiSpi_GetLastError();


#ifdef  __cplusplus
}
#endif

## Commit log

2020-02-09 Initial push - proof of concept UI is working! It can detect cameras and get/set the ISO setting.
2020-02-09 Refactored the camera stuff into a new CameraManager class, wrapped the exposure box into a spinner that supports selection-based displays
2020-02-13 Added the ARM64 libraries for SkiaSharp and libjpeg-turbo. It's probably best to keep them in the repo in case something happens to the Pi.
2020-02-16 Added crosshairs to the viewfinder, started working on the motor control layout
2020-02-19 Started modularizing the camera settings instead of hardcoding them, but this can wait until the whole thing is functional.
2020-02-19 Started working on the low-level motor control (SPI) code.
2020-02-20 Created a class for the AMT22 rotary encoders
2020-02-23 Switched to using well-sized types (like uint8_t), just better practice. Lots of work on L6470.
2020-02-23 Decided to move all of the high-level AMT22 / L6470 code over to the C# project because it's just easier to maintain. The SPI stuff will still be in C though; I made a new library called PiSpi for th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
2020-02-23 Finished moving the motor control code over to C#
2020-02-23 PiSpi was misconfigured and using old SednaMotorControl files, fixed that so they're included now
    [PiSpi.cpp, PiSpi.h]
2020-03-06 Been a while! I've been working in CAD land on the hardware side of the focusing assembly, and now I'm happy to commit it here too.
    [AMT22 Bracket.stl, Base Plate.stl, Coupling Hub.stl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]
2020-03-08 Fixed a few small bugs in PiSpi
    [PiSpi.cpp, PiSpi.h]
2020-03-08 Fixed a bug with SPI comms, added access to the motor control window
2020-03-08 Fixed a major timing problem with the way the Pi's SPI clock works when you flip back and forth between devices that use different clock polarities. This one took a while to hunt down.
    [PiSpi.cpp]
2020-03-08 Started making a focus assembly class for managing the entire focuser
2020-03-09 Finished a first pass of the focus assembly... time to see if it works!
2020-03-09 Added support to PiSpi for ignoring delays when the device is faster than the SPI clock cycle, because even delayMicrosecond(0) causes a signicant delay
2020-03-12 Fixed the L6470 code so SPI comms work now! (It requires CS to be set to high and then back to low after every byte instead of every transaction...)
    Also added some extra bugfixes to the MotorControlWindow.
2020-03-12 Got the focus control on the main page (mostly) working! It oscillates a lot at the end so i need to include some kind of PID acceleration ramp, but it works!!
2020-03-17 Started working on the schematic for the power circuit
    [Sedna Power Board.sch]
2020-03-20 Finished the 12v and 7.2v circuits, started working on the current sensing setup
    [Sedna Power Board.sch]
2020-03-26 I decided the giant monolithic PCB isn't the way to start, so I started making individual breakout-style boards for all of the SMDs. Meet v1.0 of the L6983 power board!
    [L6983 Regulator Board.brd, L6983 Regulator Board.sch, Sedna Power Board.sch]
2020-05-10 Now that the laser engraver is done, I can start fabricating some boards. Updated the power board to v1.1, put together a BOM to make 3 of them at 12v, 7.2v, and 5v.
    [BOM.xlsx, L6983 Regulator Board.brd, L6983 Regulator Board.sch]
2020-05-13 Redid the power board layout, trying a thinner but longer variant which should help cable management.
    [L6983 Regulator Board.brd]
2020-05-19 Started working on v2 of the power board - double sided, smaller, should be much easier to etch and populate for a homebrew setup.
    [Sedna Power Board v2.brd, Sedna Power Board v2.sch, Sedna Power Board.sch]
2020-05-30 v2.0.2 of the power board - still prototyping, still learning...
    [Sedna Power Board v2.brd, Sedna Power Board v2.sch]
2020-05-30 v3 of the power board, now with a trimpot on the FB voltage divider for output voltage adjustments.
    [Sedna Power Board v3.brd, Sedna Power Board v3.sch]
2020-06-01 Finished the schematic for the monitor board
    [Sedna Monitor Board.brd, Sedna Monitor Board.sch]
2020-06-06 Started working on the Monitor Board layout
    [Sedna Monitor Board.brd, Sedna Monitor Board.sch]
2020-06-07 Finished the Monitor Board v1.0
    [Sedna Monitor Board.brd, Sedna Monitor Board.sch]

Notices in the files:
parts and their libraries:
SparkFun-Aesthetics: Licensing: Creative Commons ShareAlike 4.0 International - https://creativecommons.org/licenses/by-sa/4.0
